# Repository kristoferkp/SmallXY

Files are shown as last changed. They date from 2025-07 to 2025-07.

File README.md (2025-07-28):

# Printer Sugar

### **Work In Progress!**

Printer Sugar is a fast cantilever 3D printer with quality components and a rigid frame.

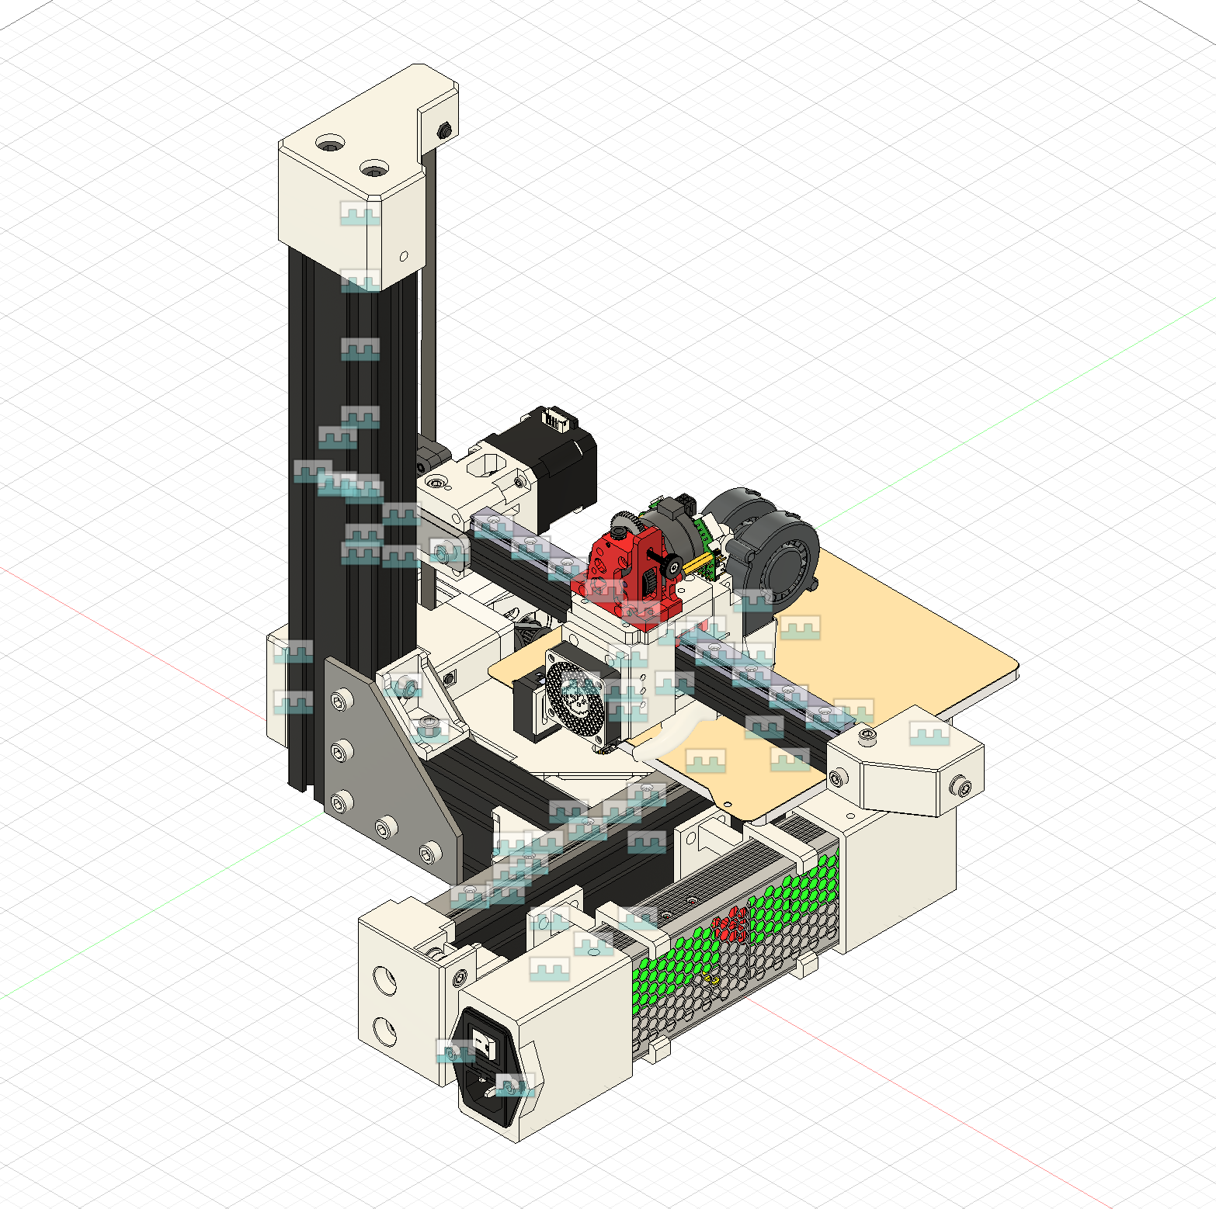
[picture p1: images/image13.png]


## Features
- Cartesian with belted Z
- Compact size
- 180x180x180mm build volume
- Easy to assemble
- No drilling
- Runs Klipper
- Super fast bed meshes with BTT Eddy sensor
- Toolhead CAN board
- Driven by the affordable BTT SKR Pico
- Quality components
- Easy to build

## BOM
|Part|Notes|Qty|Price (EUR)|Shipping|Total Price|Link |
|---|---|---|---|---|---|---|
|TZ V6 2.0 hotend | |1  |15,17 € |0,00 €  |15,17 € |https://www.aliexpress.com/item/1005008625753387.html |
|HGX Lite extruder | |1  |22,45 € |0,00 €  |22,45 € |https://www.aliexpress.com/item/1005008095324836.html |
|Raspberry Pi |already have one on hand |0  |0,00 € |0,00 €  |0,00 € |https://raspberrypi.com |
|BTT SKR Pico 1.0 | |1  |22,63 € |0,00 €  |22,63 € |https://biqu.equipment/products/btt-skr-pico-v1-0?variant=40565262188642 |
|BTT Eddy Coil | |1  |12,76 € |0,00 €  |12,76 € |https://biqu.equipment/products/bigtreetech-eddy?variant=41018205405282 |
|Fystec UCAN |cheaper to buy this with the eddy coil than duo|1  |6,31 € |0,00 €  |6,31 € |https://www.aliexpress.com/item/1005006834027165.html |
|BTT EBB36 | |1  |14,46 € |0,00 €  |14,46 € |https://biqu.equipment/products/bigtreetech-ebb-36-42-can-bus-for-connecting-klipper-expansion-device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|
|5015 Blower Fan | |2  |2,76 € |0,00 €  |5,52 € |https://www.aliexpress.com/item/1005002488988359.html |
|ADXL345 |for bed |1  |2,72 € |0,00 €  |2,72 € |https://www.aliexpress.com/item/1005006825808074.html |
|4010 Fan | |3  |2,51 € |0,00 €  |7,53 € |https://www.aliexpress.com/item/10000382046169.html |
|2M PTFE tube |ID2 OD4 |1  |3,92 € |0,00 €  |3,92 € |https://www.aliexpress.com/item/1005006242932887.html |
|IEC320 C14 |AC-08 |1  |2,37 € |0,00 €  |2,37 € |https://www.aliexpress.com/item/32961436466.html |
|Mean Well UHP-350-24 | |1  |59,12 € |0,00 €  |59,12 € |https://www.digikey.ee/en/products/detail/mean-well-usa-inc/UHP-350-24/7707254 |
|180x180 bed |with magnetic plate |1  |22,58 € |0,00 €  |22,58 € |https://www.aliexpress.com/item/1005005641707683.html |
|MGN15H 250mm | |2  |12,50 € |0,00 €  |25,00 € |https://www.aliexpress.com/item/1000007480470.html |
|MGN12C 250mm | |1  |10,09 € |0,00 €  |10,09 € |https://www.aliexpress.com/item/1000007480470.html |
|Nema 17 motors 40mm |3pcs |1  |45,03 € |0,00 €  |45,03 € |https://www.aliexpress.com/item/1005006568308689.html |
|Silicone spacers 4pcs |16mm |1  |3,14 € |0,00 €  |3,14 € |https://www.aliexpress.com/item/1005001823789355.html |
|GT2 Loop Belt 188mm |6mm width |1  |2,67 € |0,00 €  |2,67 € |https://www.aliexpress.com/item/1005006417199222.html |
|GT2 Loop Belt 650mm |9mm width |1  |2,01 € |4,59 €  |6,60 € |https://www.aliexpress.com/item/32805615376.html |
|5x8x1 shim |comes in a pack of 20 |1  |1,08 € |2,87 €  |3,95 € |https://www.aliexpress.com/item/1005004050860540.html |
|F695 2RS bearings |pack of 10 |1  |6,37 € |0,00 €  |6,37 € |https://www.aliexpress.com/item/32850989216.html |
|GT2 20T pulley 6mm | |1  |4,48 € |0,00 €  |4,48 € |https://www.aliexpress.com/item/32995102911.html |
|GT2 20T idler 9mm | |1  |3,43 € |0,00 €  |3,43 € |https://www.aliexpress.com/item/1005005781354110.html |
|GT2 20T pulley 9mm | |1  |1,35 € |5,04 €  |6,39 € |https://www.aliexpress.com/item/32348909911.html |
|GT2 80T puley 6mm | |1  |4,85 € |2,79 €  |7,64 € |https://www.aliexpress.com/item/1005005585888163.html |
|5x70mm shaft with flat spot| |1  |2,22 € |5,37 €  |7,59 € |https://www.aliexpress.com/item/1005008459963157.html |
|F695ZZ bearing | |1  |3,40 € |0,00 €  |3,40 € |https://www.aliexpress.com/item/1005006822749704.html |
|695ZZ bearing | |1  |3,24 € |0,00 €  |3,24 € |https://www.aliexpress.com/item/4000909556973.html |
|3060 extrusion |350mm |1  |10,57 € |0,00 €  |10,57 € |https://hobby-store.pl/en/aluminium-profile-3060-type-t-slot/altrax-aluminium-profile-3060-t-slot-matt-black.html |
|3060 extrusion |280mm |1  |8,46 € |0,00 €  |8,46 € |https://hobby-store.pl/en/aluminium-profile-3060-type-t-slot/altrax-aluminium-profile-3060-t-slot-matt-black.html |
|3060 extrusion |120mm |1  |3,62 € |0,00 €  |3,62 € |https://hobby-store.pl/en/aluminium-profile-3060-type-t-slot/altrax-aluminium-profile-3060-t-slot-matt-black.html |
|L-type connection plate | |2  |4,00 € |0,00 €  |8,00 € |https://www.aliexpress.com/item/1005008549907378.html |
|T-type connection plate | |1  |4,46 € |0,00 €  |4,46 € |https://www.aliexpress.com/item/1005008549907378.html |
|3030 Corner brackets | |1  |7,56 € |0,00 €  |7,56 € |https://www.aliexpress.com/item/1005007540170351.html |
|M3 countersunk 30mm | |0  |3,69 € |0,00 €  |0,00 € |https://www.aliexpress.com/item/1005007838338973.html |
|M3 screw set | |0  |10,34 € |0,00 €  |0,00 € |https://www.aliexpress.com/item/1005007159750547.html |
|M3 heatset insert |M3x5x4 |0  |3,95 € |0,00 €  |0,00 € |https://www.aliexpress.com/item/1005007973137842.html |
|M3 heatset insert |M3x4.5x5 |0  |2,92 € |0,00 €  |0,00 € |https://www.aliexpress.com/item/1005003582355741.html |
|M5 screw set | |0  |13,36 € |0,00 €  |0,00 € |https://www.aliexpress.com/item/1005007268850289.html |
|M5 50mm | |0  |4,52 € |0,00 €  |0,00 € |https://www.aliexpress.com/item/32810872544.html |
|M6 screw set | |0  |14,75 € |0,00 €  |0,00 € |https://www.aliexpress.com/item/1005007268850289.html |
|M6x12mm | |0  |4,11 € |0,00 €  |0,00 € |https://www.aliexpress.com/item/1005007632215508.html |
|M8 30mm | |0  |3,72 € |0,00 €  |0,00 € |https://www.aliexpress.com/item/32810872544.html |
|3030 M6 t-nuts | |0  |5,58 € |0,00 €  |0,00 € |https://www.aliexpress.com/item/1005007587044629.html |
|2020 M5 t-nuts | |0  |3,13 € |0,00 €  |0,00 € |https://www.aliexpress.com/item/1005007587044629.html |
|Spade crimping kit | |0  |21,92 € |0,00 €  |0,00 € |https://a.aliexpress.com/_EJTbUyW
|16AWG wire | |0  |4,41 € |0,00 €  |0,00 € |https://a.aliexpress.com/_EGvjSkQ
|XH 2.54 kit | |0  |3,41 € |0,00 €  |0,00 € |https://a.aliexpress.com/_EvVOt9y

## Credits
- Big thanks to the Ratrig community and the team behind Ratrig for the inspiration and refrence for the design.
- EVA toolhead community and team for the refrence for my toolhead.
- Voron community for the insipiration of the CoreXY design and refrences.
- BigTreeTech for the refrence parts of their products.
- GrabCAD community for some refrence parts.

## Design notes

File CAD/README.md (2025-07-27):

# CAD files

The f3z is a Autodesk Fusion archive. I would recommend to open it in a new folder as there will be a bunch of files in there when uploaded.

The STEP files are there for compatibility. Do note, that there isn't version history included in the step file.

See the Cantilever files for the design.

## The CoreXY

The CoreXY was not and still isn't finalized. Please do not try to build one as it is incomplete. It is there to show that I actually did something and did not snooze all day.

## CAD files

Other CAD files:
CAD/CoreXY.step
CAD/Cantilever.step
CAD/Cantilever.f3z
CAD/CoreXY.f3z

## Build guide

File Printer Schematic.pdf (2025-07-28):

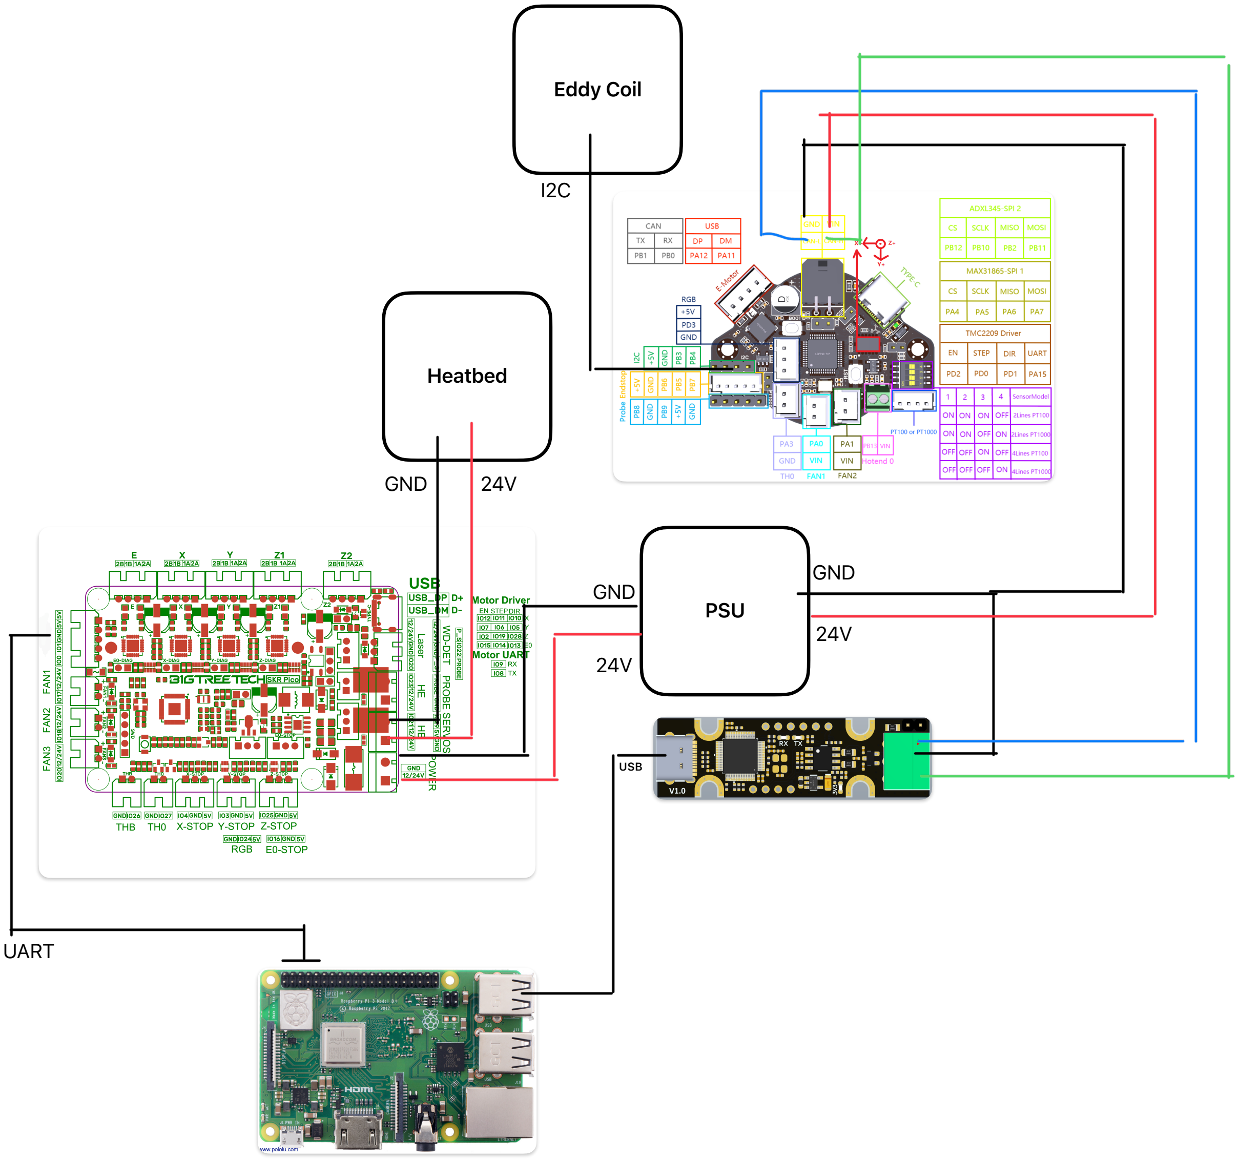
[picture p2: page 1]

USB

UART

PSU

GND

24V

GND

24V

Heatbed

Eddy Coil

I2C

GND 24V

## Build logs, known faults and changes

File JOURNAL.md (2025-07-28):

---
title: "Printer Sugar"
author: "Kristofer P"
description: "A fast and sturdy cantilever 3D printer"
created_at: "2025-07-07"
---

### Total time spent on project at the submitting mark: around 67h

My school doesn't have a 3D printer (well it does but it is a broken Makerbot Replicator) so I wanted to change that. With the 350 USD budget from Hackclub I can design a printer that my fellow schoolmates can use to make their designs come to life.

The after many hours of back and fourth I decided that the printer will use CoreXY kinematics for its great speed and compact size.

# 1st entry: July 7th, 2025: Initial research and frame design.

Researching what parts to include in the 3D printer was a tough challenge to say the least.

First, I wanted to build a small coreXY printer, but after searching for the parts online (mainly AliExpress) and seeing what I already have on hand (basically nothing apart from a Raspberry Pi), I came to the conclusion that it will blow the $350USD budget.

So then, I decided to build a cantilever design for its simplicity and cost.
The main problem that seems to plague cantilever printers is instability.

As I wanted to build a fast machine, hopefully beating the Bambu Lab A1 mini, I decided to use 2040 aluminium extrusion as it is cheap and will probably give it the stability it needs.

I set my target to the Bambu Lab A1 mini. With its 180x180x180mm build volume, my machine would need to match that.

The heatbed options aren't very big on AliExpress (I found very little listings for 180mm heatbeds), so I decided to use a heatbed meant for the Micron+ printer.
There was a option of just using the Bambu Lab A1 mini heatbed unit as its price is very reasonable at €42, but with Bambu being so locked down, I couldn't find any information on it.
It probably is a 24V about 100W heater and some mystery thermistor. I would need to get my hands on one to find out.

I also searched for linear rails and landed on the MGN12H at 250mm long. They should be long enough for the 180mm bed and mounting stress. But I might swap them out for beefier rails down the line.

Found NEMA17 motors that should have enough torque to hold the X-axis up not during use. 17HS4401S.

Chose to use roll-in t-nuts for the linear rails. They are a bit more expensive than drop-in ones, but are way to save the hassle later on when building.

That was the end of the reasearch on that day.

---

I started off by searching for some 2020 and 2040 extrusion. Eyeballed the lengths to be 350mm for the Z, 150mm and 300mm for the bed, 400mm for the X-axis.

The extrusions will be joint together with joining plates. Maybe I will add some other joints, tbd.

Then I added the linear rails. The grabcad model was only 100mm long, so I had to extend it to 250mm. 

I do not know why, but Autodesk Fusion was playing tricks on me the entire time.

For the life of me, I couldn't understand why Fusion was chopping off parts of the entirely different bodies from different compontents.
When I tried splitting the 100mm rail to 50mm, it would split every single rail part and then when I went to delete the extra 50mm, the rail would suddenly have holes in them.

It happend in other areas too, like the extrusions. When I went to extend or cut an extrusion, the other extrusions would cut themself too.
I ended up somehow forcing myself through the problem, so if anyone has some ideas, let me know.

### Time spent on that day: 5h

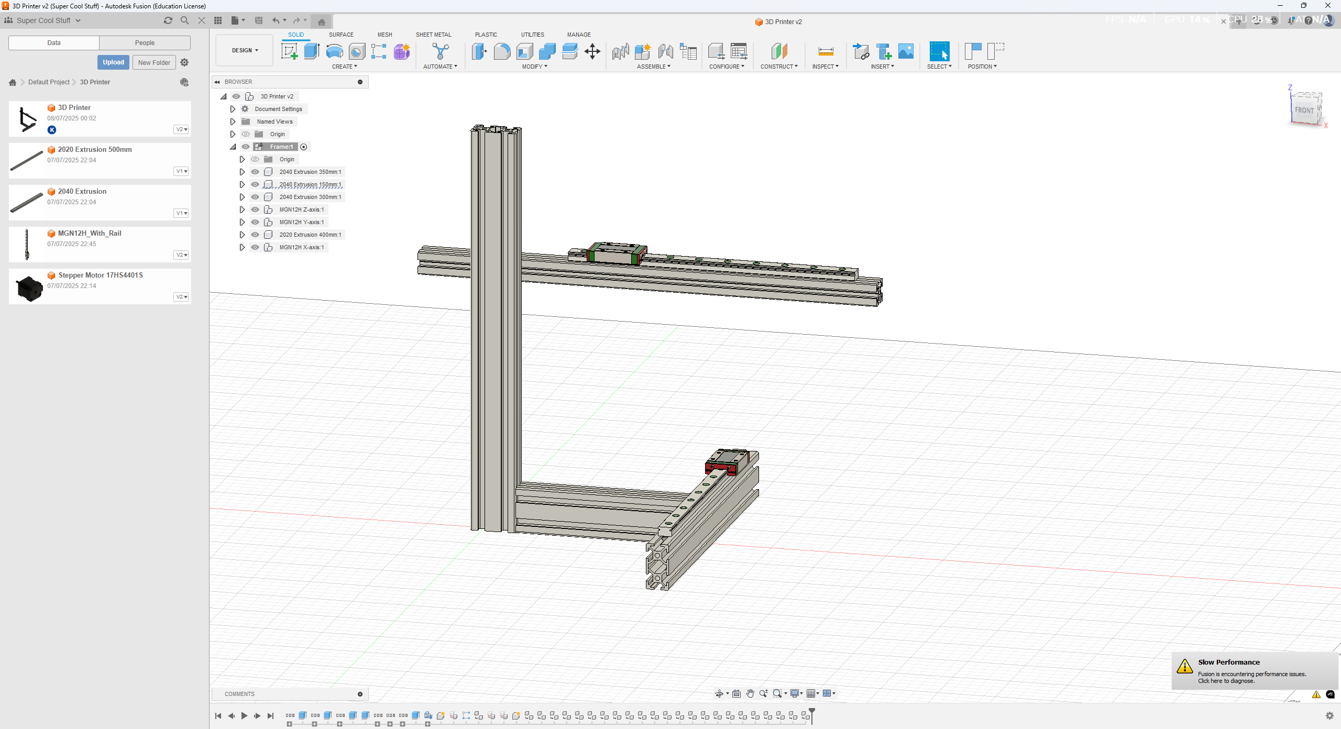
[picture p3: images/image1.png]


# 2nd entry: July 8th, 2025

Did some searching and came to the conclusion, that 2040 extrusion is too flimsy and decided to swap out the extrusions for 3060.
I also searched where I can buy the extrusions and found a Polish shop that sells custom lenghts for a really reasonable price.

3060 for €0.30/cm and 2020 for €0.12/cm.

The bed has been a quite the headache. I can't really make my own bed as I do not have the equipment necessary, so I need to buy one pre-drilled and tapped.

I did find a Ratrig V-minion heatbed assembly, but noone has bought it so it is kinda risky.
The other option I found was the Micron180 heatbed assembly.

It has all the necessary things included for €60, but I might need to swap it out later when I optimize the BOM.

The Micron has a slight flaw for my use case, it is designed to be mounted fixed to the bottom of the printer. Which means, the mounting bracket that goes between the bed and the linear rail carriage has to be huge.

---

I started the day off with replacing the extrusions and fighting with Fusion a bit. I have managed to make sense of the problem a bit, but still kinda wonky.

The rails were next. They were less of an issue, but with the Fusion magic again, I am having a hard time categorizing the models into components. Please do not inspect the components too close.

The mounting brackets were next. I did several designs and L-shaped mounting brackets that I found on that Polish website seems to be the best. I did add a T-shaped bracket to the bottom and normal corner brackets for reinforcment.

I found the CAD model for the Micron180 and just took the bed assembly out of the file. ;)

I did have to modify it, removing the extrusions, making a carrier plate for it, etc.

The carrier plate might actually not warp, I need to learn how the Fusion simulation works.
I have a feeling it will not hold up.

### Time spent on that day: 7h

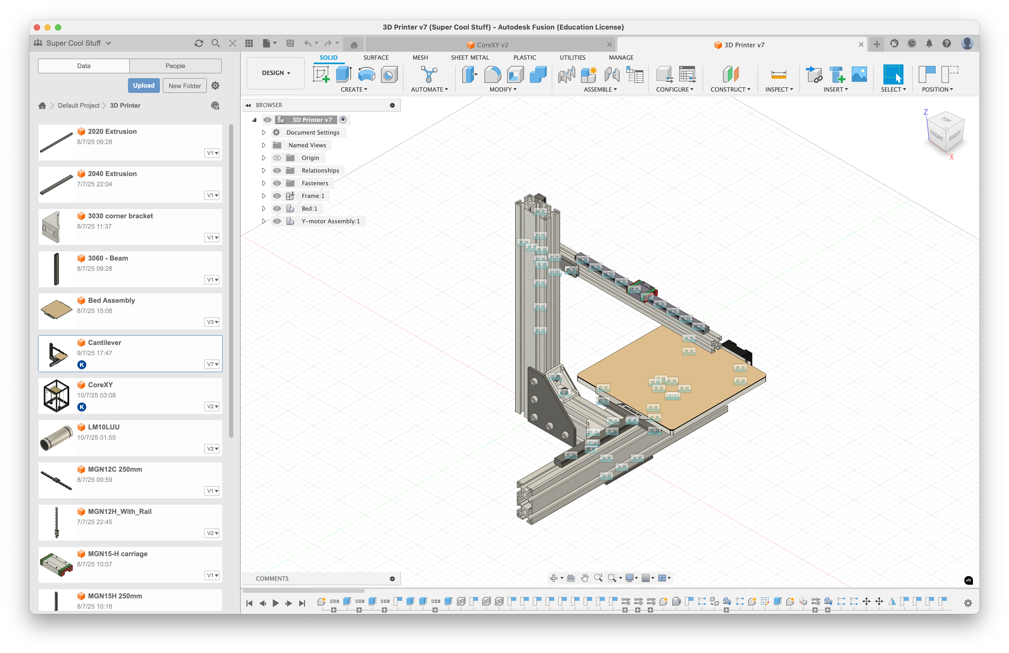
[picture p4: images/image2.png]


# 3rd entry: July 9th, 2025

I started the day researching again.

Looking over the BOM and the design, I think I can build an CoreXY for not a lot more and a lot faster and probably safer design wise.

The bed on the cantilever design is really suspicious.

I decided that I will make a flying bed and not a flying gantry.

The Z will use 4 linear rods and 2 Z-motors with screws.
This is because I only have 2 Z-motor drivers on the board and beacuse it is cheaper.

The Z will use 10mm linear rods, LM10UU and Nema17 motors with lead screws on them.

Hoping to find motors that aren't that expensive.

Found basically Prusa MK3 Z motors with built in 300mm lead screws, will use those.
They come on the printer in a 2 pack too, which is kinda amazing. The stars are slightly aligning.

There is a posibility of using some more Prusa motors. That makes the project a bit more accessable (if someone has MK3 motors lying around).

It is possible to use the MK3 bed and Y-carriage as well, but I don't have them and they are more expensive than the Micron180 bed I want to use.

The beds should be replaceable with a few design tweaks.

I also made the BOM a bit more complete and I am going to have to source a few parts myself beacuse the BOM is offically blown out of budget.

---

I started doing the CAD for the CoreXY printer.

I decided to use 2020 extrusion as there is more of it, so the rigidity shouldn't be a problem, and it is quite a lot cheaper.

The bottom of the printer is under review. I might make a skirt for the electronics or I house the electronics at the back of the printer.

I got the linear rods placed, the bed placed, the NEMA17 motor and its accompanying lead screw and the lead nut placed.
The second linear rods used to connect the lead screw and the Z-axis linear rods were also placed.

Next up I need to make the connecting piece that will be 3D printed.

I have realised that I really do like tinkering in Fusion and researching the parts. It is quite hard, but I like the challenge.

Aimlessly modeling is very time consuming, but when I achive the aim, it gets quite rapid.

### Time spent that day: 8h

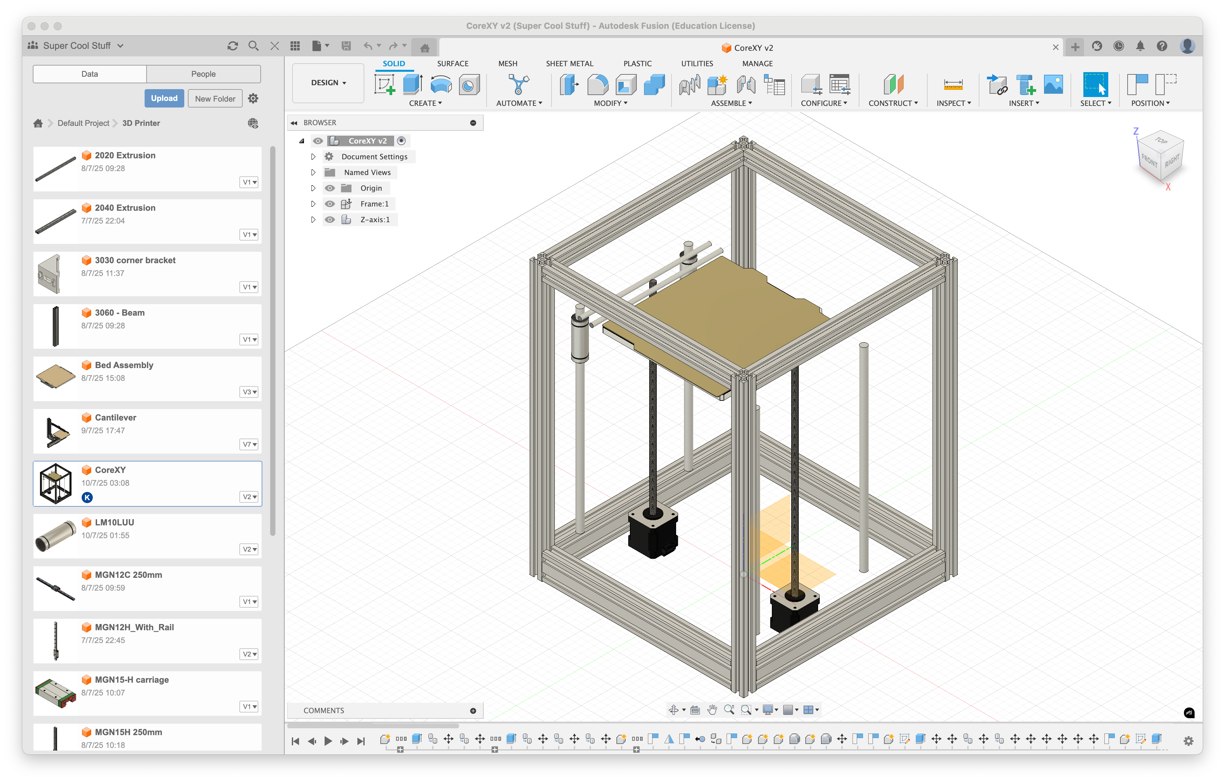
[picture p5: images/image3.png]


# 4th entry: July 10th, 2025

Still thinking about the design of the printer.

The SKR Pico 1.0 that I would like to use beacuse it is so cheap and there is a possibility of using a CAN transiver so you do not have to buy a seperate CAN board.

The SKR Pico has 5 motor drivers - Extruder, X, Y, Z and Z2.

When researching Z axis beds on other printers, I realised that having 3 Z-motors would be advantageous beacuse the bed could trim itself. There would be no need to trim it yourself, just use the Z_TILT_ADJUST in Klipper, just like the Voron Trident.

Then I thought to myself, would I need to swap out the SKR Pico for a board that has drivers for the Z.

But then I realised, if I use a CAN toolhead board, it has a built in TMC2209 for the extruder - I don't need the extruder driver on the board anymore, so I can use that for the 3rd Z motor.
I did some searching (asking AI) and it is indeed feasable.

I then decided to change out the Z axis design again for the Voron Trident design.

I went to the Trident configurator and for a build size of 180mm^3 it recommended me the frame size of 340x340x430mm - basically the frame size I was already using.

I searched a lot on aliexpress too. I think I had over 100 tabs open at the same time (thank you Zen browser for saving me a bit).

I went down a different rabbit hole of "what if I pivot again and build a cartesian?" but that I shut down as there isn't really any reason to pivot again.

I searched about all the different motors out there. There are a lot of them.

But they have quite awful shipping times. If I buy them now, it will take almost a month to get to me. This is also the reason why I am crunching so hard. Time is of the essense.

I watched a cool video about how to build a 3D printer, it is a bit old at this point (5 years at the time of writing), but still quite a good watch. 
[How to Build a 3D Printer (The Ultimate Guide)](https://www.youtube.com/watch?v=qub5chyIQ0s&t=5674s)

I was really worried about the shipping costs on the motors. They ballooned way out of porpotion. 
I was really doubting if there are any cheap motors out there, but then I found Robotdigg.

It is quite a cool site and they had the motors with lead screws that I needed, the shipping was around 30 euros.

I wasn't satisfied yet. Over 120 euros just for Z-axis motors is just too much on a somewhat budget printer.

I had my eye out for the motors on the BOM, but there was a small issue - I could only buy one.
That made me search for better option, but there weren't any and then I circled back to these.

I do not know what kind of trickery AliExpress does some times, but when I opened the tab in incognito, I finally was able to buy more than one.

The price is around 4 euros more, but I would have liked an option to discard that promotion so I could buy more of them.
There should have been a pop up that said "Hey, I see you are trying to buy more than 1, would you like to get rid of that exclusive offer?"

But I digress, I finally got some cheaper motors for the Z-axis but the tomfoolery wasn't done just yet.

The A/B motors were also quite the challenge. I searched far and wide for the motors that ended up in my BOM, none were quite good enough. Not enough torque, too hi inductance, not enough current, etc.

There was the shipping problem here as well. As soon as you ordered more than one, the shippiing shot up to around 30 euros. This was double the price of the motors together, so I had to find some other ways.

The way ended up pretty simple. Find some that come in a pack. This eliminates the shipping cost on pretty much in all cases.

I found the 17HE19-2004S motors. They are powerful, have a pretty low inductance and are cheap. They only come in a pack of 3, not 2 that are needed - so I guess one is extra just in case.

---

I started the CAD redesign by removing everything. This day has been heavy on the modelling side.

I remade the entire frame. Slightly modified the dimensions. 

I added the backbrace to the frame for the 3rd Z motor.

I added the linear rails, the stepper motors with the lead screws.

I added the bed, the aluminum braces under it.

I did take the bed holder mechanism from the Voron Trident, very many thanks to the team and the contributers that make that project happen.

As my bed is quite a lot smaller than the Voron Trident's bed, I had to modify half the mechanism to work with my smaller bed as there is enough room for the big and bulky mechanism.

Should have I made the frame bigger? I guess we have to find out.

The margins on the parts are still quite small, maybe even hitting the aluminum bed, I will have to find out when I build the machine and modify it a bit.

Added 3-way corner connectors to the build.

Started designing the gantry.

### Total time spent that day: 8h

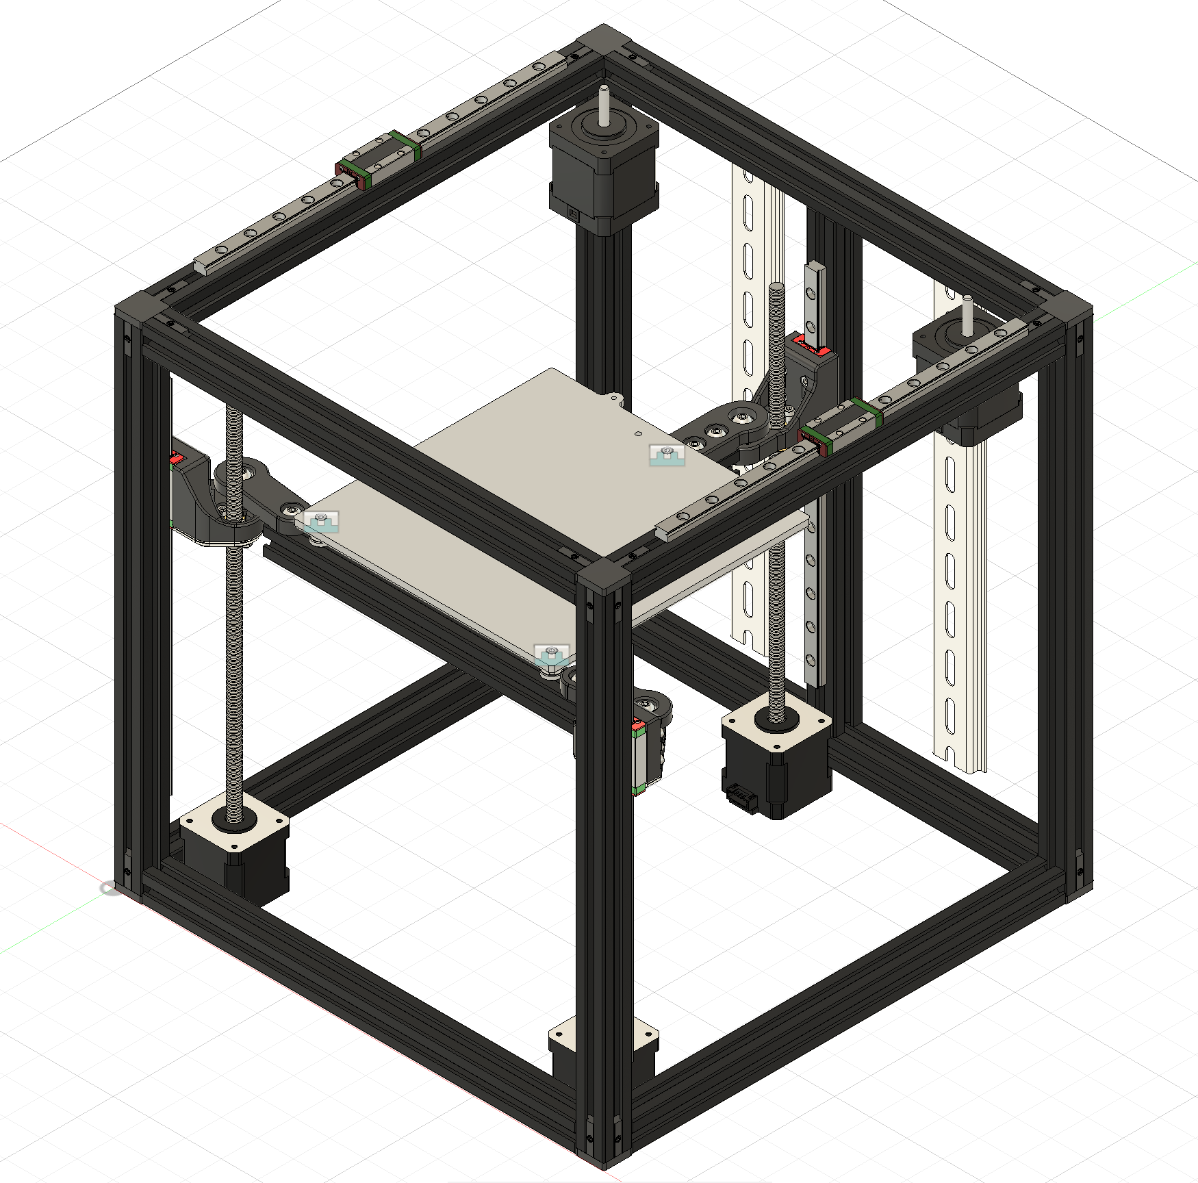
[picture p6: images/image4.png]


# 5th entry: July 11th, 2025

Oh how many different options. I started questioning the corner connectors. Are they even good for a 3D printer? Are these the better option?

I didn't want to use blind joints as they require drilling new holes into the extrusion that I am personally not confortable doing. I could figure it out but I don't want to risk it.

Then I saw the openbuilds corner cubes. They seem good and sturdy. Tapping the ends of the extrusions doesn't seem all that difficult. I was ready to add them to the design when I found out how expensive they are.

I mean they aren't that expensive, but still are quite a bit more expensive than just using corner brackets.

I have to use corner brackets anyway for the bed frame so might as well use them all throughout.

20pcs with hardware is 12 euros as supposed to corner cubes with are 14 euros for 8pcs.

---

I started by replacing all the frame extrusions again. I saw that there are differences from extrusion manufacturer to another in [a YouTube video about blind joints](https://youtu.be/2dvbn0rWA60).

I found the technical drawings of the manufacturer on the [Polish webstore where I found the extrusions](https://hobby-store.pl/) and I started to create a sketch, made almost halfway to a finished sketch and then I found they just have a 3D model available...

I downloaded it and replaced all extrusions on the design with the new one. They are indeed different but not by much and I really doubt it was neccessary.

Started making the gantry.

### Total time spent that day: 5h

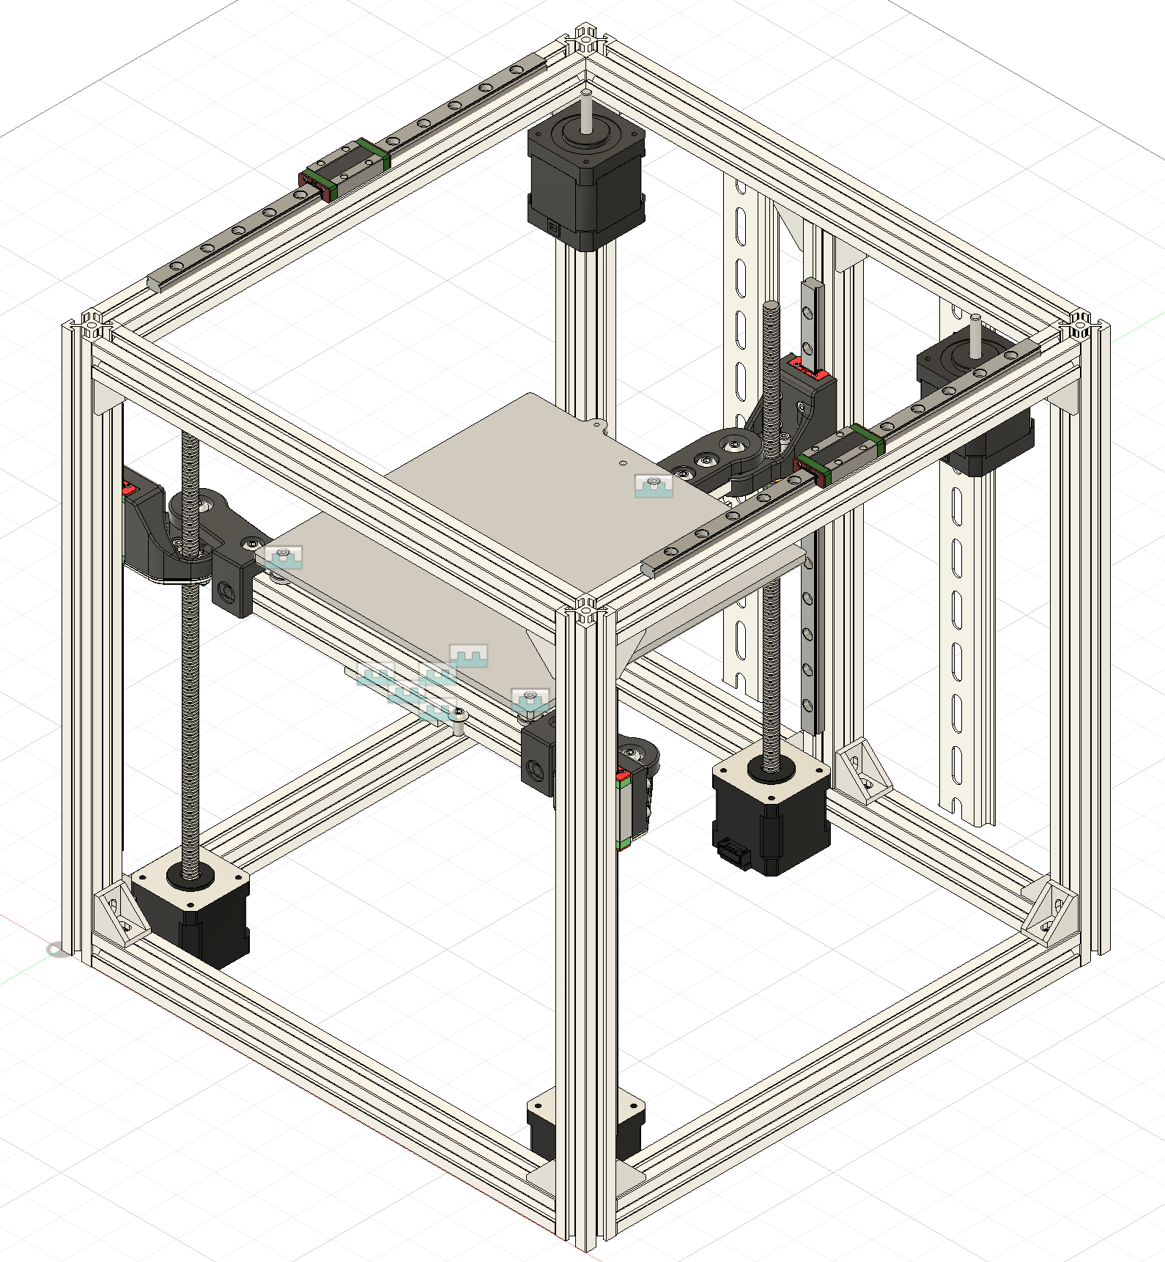
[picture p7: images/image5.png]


# 6th entry: July 12th, 2025

Today started off different. No researching, just modelling.

Made the X-gantry belt/extrusion holder.
It was actually not that bad. I found models for heatset inserts, F695 bearings.

The real complexity came when I finished the gantry and noticed that I do not have enough room in front of the bed for the toolhead.

As I want to use the eddy probe and use the tapping functionality in the [eddy-ng project](https://github.com/vvuk/eddy-ng), the toolhead needs to fit over the bed.

This would not have been possible with the current design, so I needed to make the frame bigger.

This meant a lot of backtracking and modifying the existing design.

Uhmm, this is kinda weird. After coming back to this, I got recommended a ModBot YouTube video exactly about eddy-ng. Perhaps he saw the project the same way I did, Voron discord server.

The A/B motors mounts were next. They were pretty complex, I am doubting my abilities to create a working model, but when I get my hands on the parts and assemble it, I can tweak the models.

I had to figure out how to make the belt tensioner. I first thought of a way where the motors move, but then I thought of a system where the front pulleys get pulled closer to the front.

When I had done those, I went and made the electronics bay. I found a model of MeanWell PSU I am planning to use, but as the electronics bay uses DIN rails, the mounts are easily interchangeable.

The diary entries get shorter and shorter as I have less and less time, but I still have managed to crunch my way through. I just need to make the toolhead, finish the electronics and the BOM.

I want to add a nozzle scruber to the bed assembly too, but that stage comes a bit later.

That is about it for today. I kinda need to fix my sleep schedule, all these late night CAD sessions aren't probably good for me.

### Total time spent that day: 8h

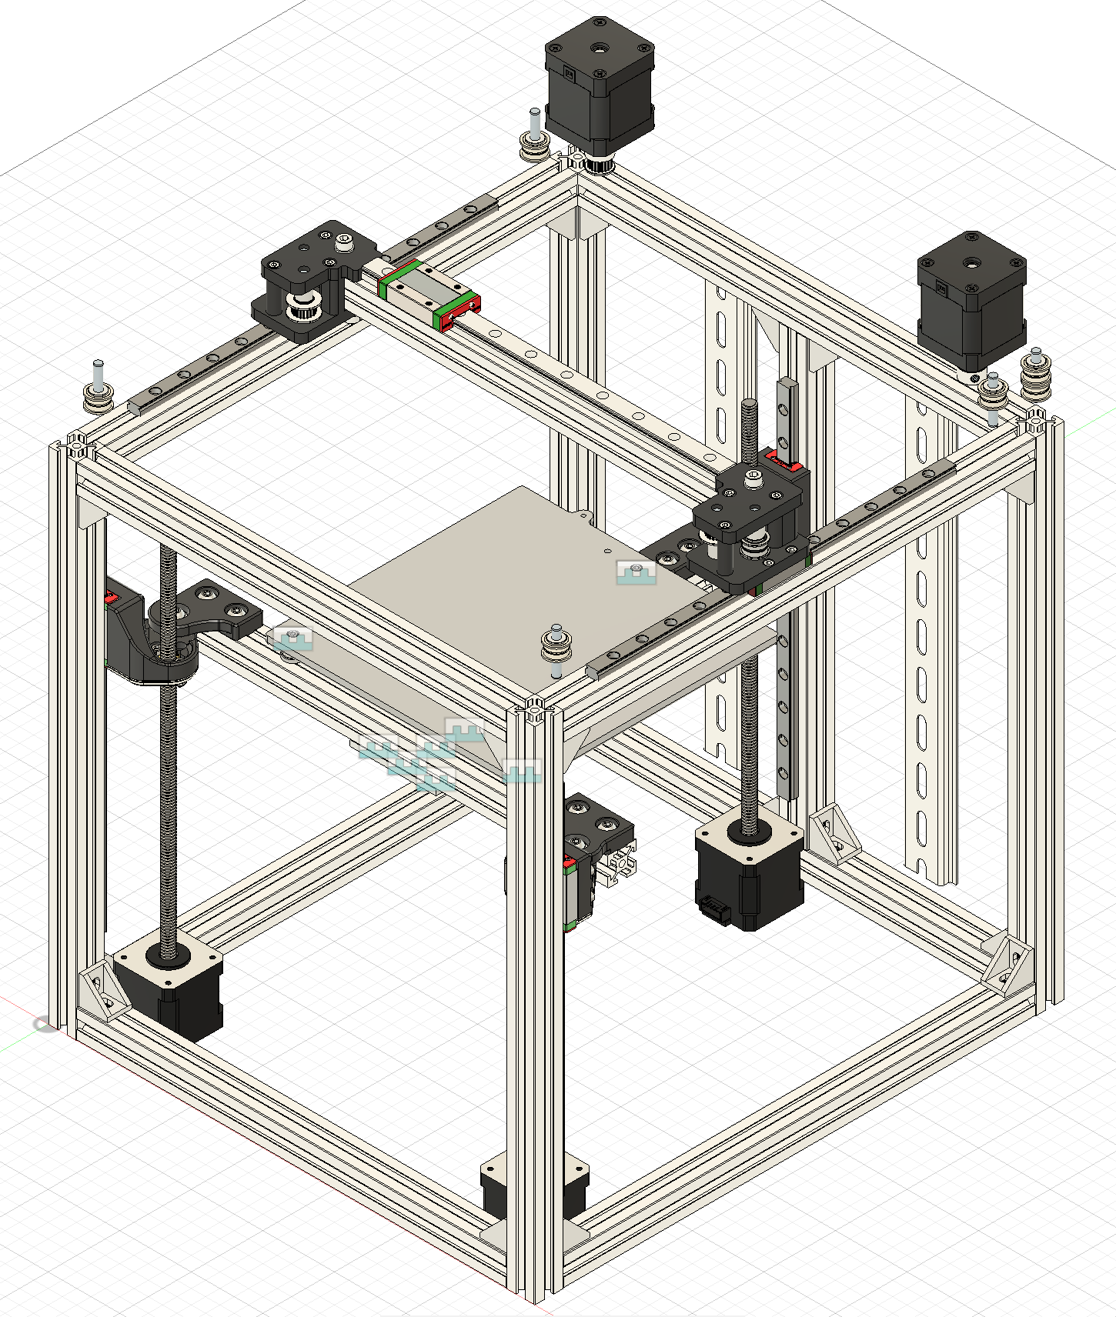
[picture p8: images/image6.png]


# 7th entry: July 13th, 2025

Finished the CoreXY printer, but when looking over the BOM it is really expensive. I might choose to change it out to cartesian platform or even go back to cantilever.

Spent a lot of time researching on how to make the CoreXY cheaper, but to no avail. Still seems too expensive.

After that I made the decision to move to a cartesian platform.

I made the frame out of 3030 extrusion for the cartesian printer, but the problem is joining the extrusions together, the frame needs blind joints, but I do not know if I can do it. Would love it if I didn't have to do blind joints.

Need to reaserch a bit more.

### Total time spent that day: 2h

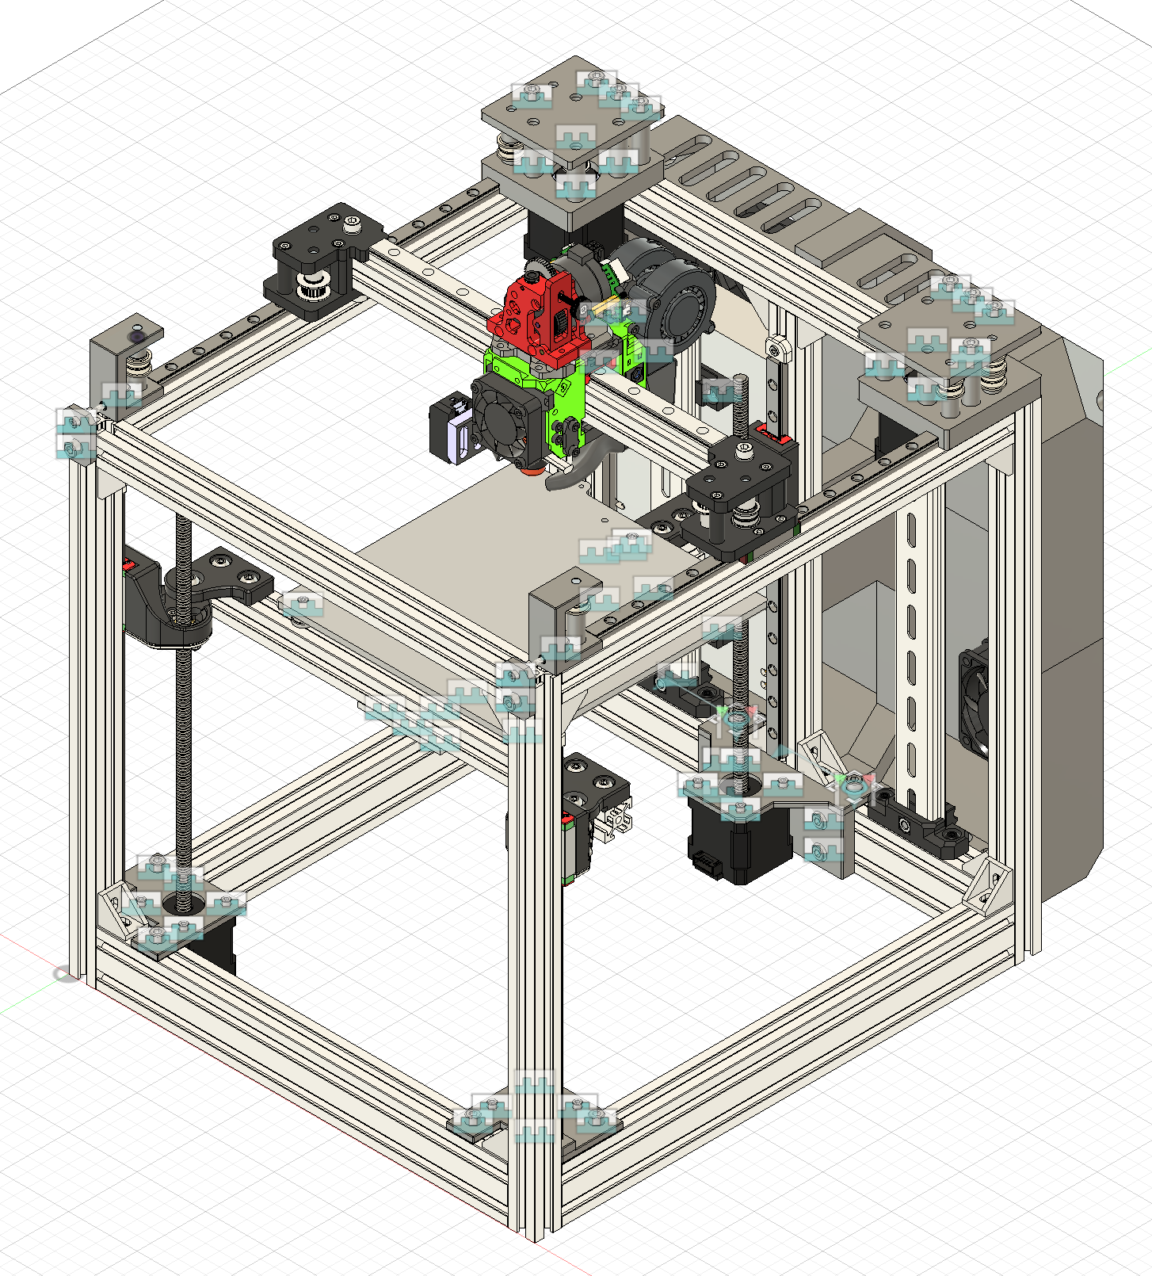
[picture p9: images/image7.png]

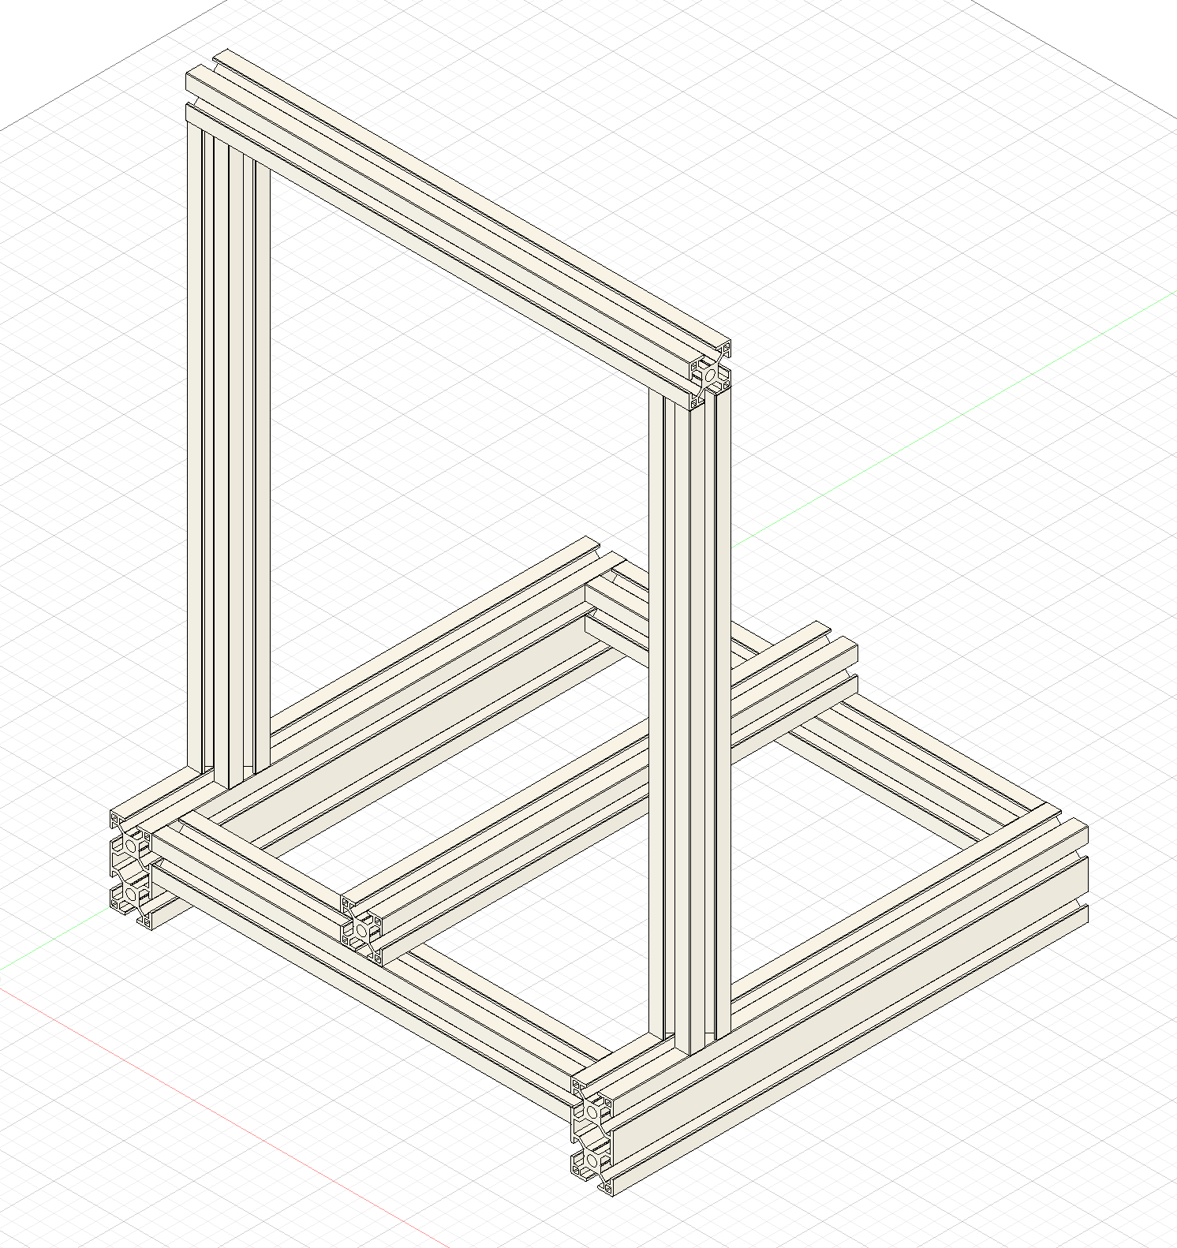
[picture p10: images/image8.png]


# 8th entry: July 14th, 2025

Started with research. How do save costs on a 3D printer while still maintaining speed?

Saw that the RatRig V-minion is a good printer with good speed, but it is not available anymore and is a bit too expensive.

Decided to make a cantilever design inspiried by the V-minion. I do not like that it has a lead screw Z and would like to make the electronics mount on the printer and not be on a seperate box.

### Total time spent that day: 2h

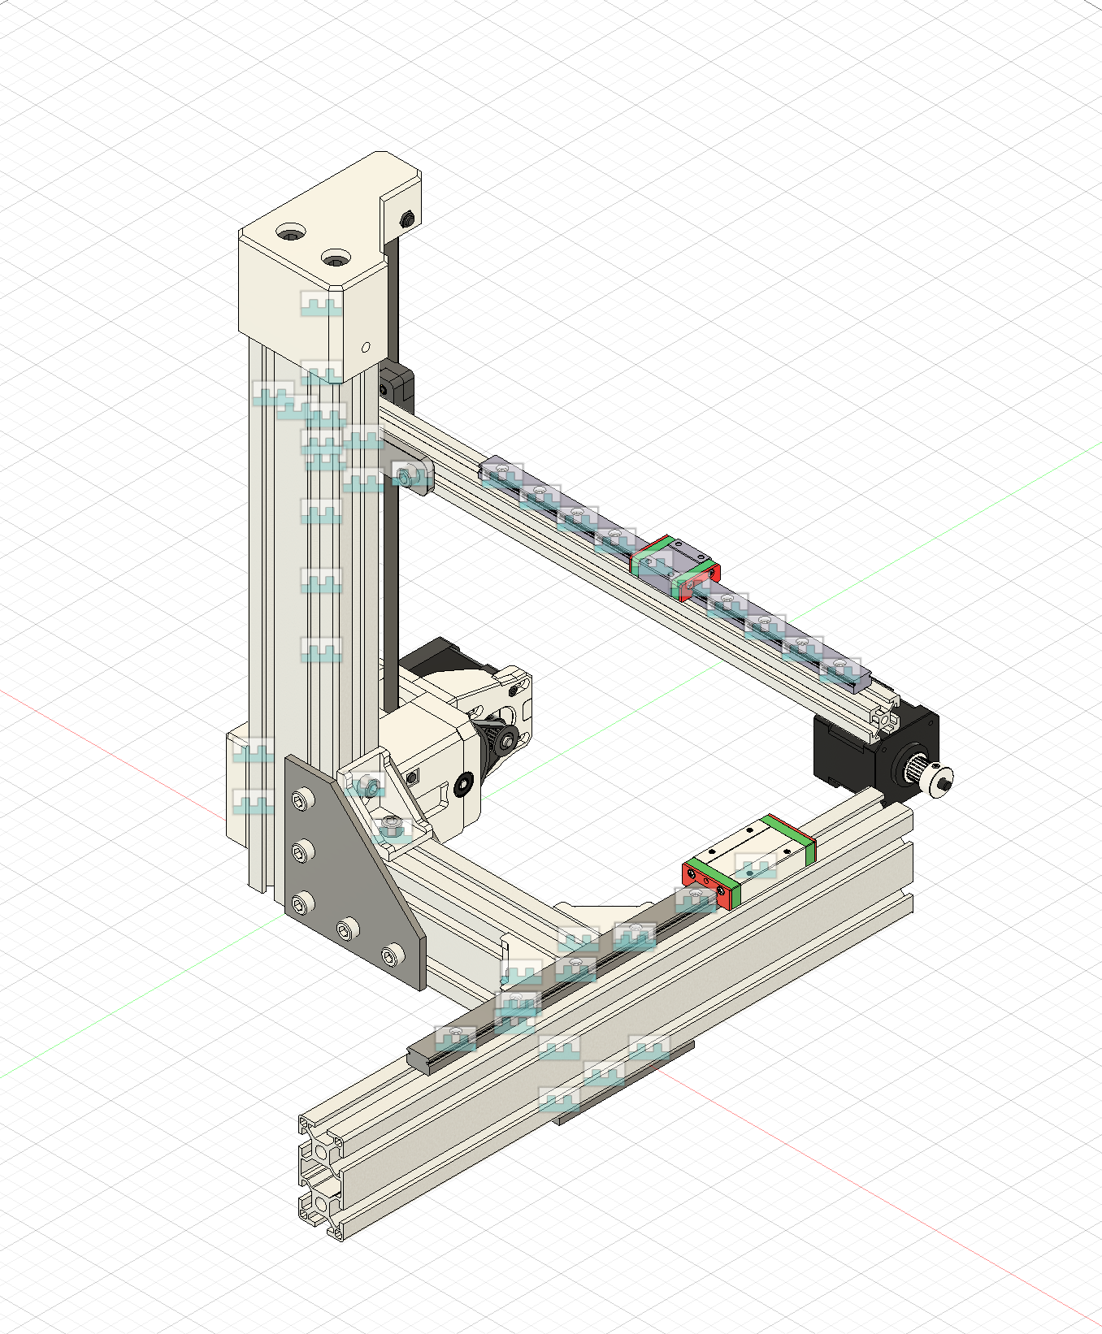
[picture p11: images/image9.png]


# 9th entry: July 15th, 2025

Made some improvements to the printer. The Z axis is belted, the bed is still 180x180mm big, but the footprint is smaller.

Started making the z axis and bed. 

Saw from the Micron180 that the Z-axis should have a gearbox of some sorts to stop the X-axis dropping down.

Decided to make the gearbox similar to the one on the Micron. I will adapt that onto the cantilever printer.

The bed was quite simple. I found a 180x180mm bed for cheap. The Lerdge iX print bed. Its heatbed is only about 25 euros and has the mounting holes close together, so the plate under it doesn't need to be that big. 

The problem with the bed is that it is quite thin and doesn't have the power of a silicone heater, but I think that it will be good enough.

The plate should be made from aluminium, but that is quite expesive, so I think I will try and make it using carbon fiber infused filament.

Search for suitable filaments and found the PLA-CF from Bambu Lab. It doesn't have the bending modulus of something like Nylon, but it is pretty close.

Bending modulus is the bending force the filament can withstand - or so I think.

I just need to add some silicone spacers so the hot bed doesn't touch the plate. Might still need to make the plate out of aluminium if this doesn't work.

I uploaded the plate design to JLCCNC and the quote was around 20 euros plus shipping. Not too bad, but that still would eat into my budget more than I would like it to.

I found the JLCMC website, even though I have ordered from JLCPCB in the past, never have my eyes wondered so far that I find this website. Looks cheaper than AliExpress but I will have to search this site longer at a later date.

I can get a whole Voron 2.4 350mm spec frame for 20 EUROS! My jaw dropped when I saw that.
Literally a similar frame on AliExpress is 77 euro. Holy moly. What a find. 

The best part is the global direct line shipping took me like under a week the last time I ordered from JLCPCB. I have to find out more about this website.

### Total time spent that day: 2h

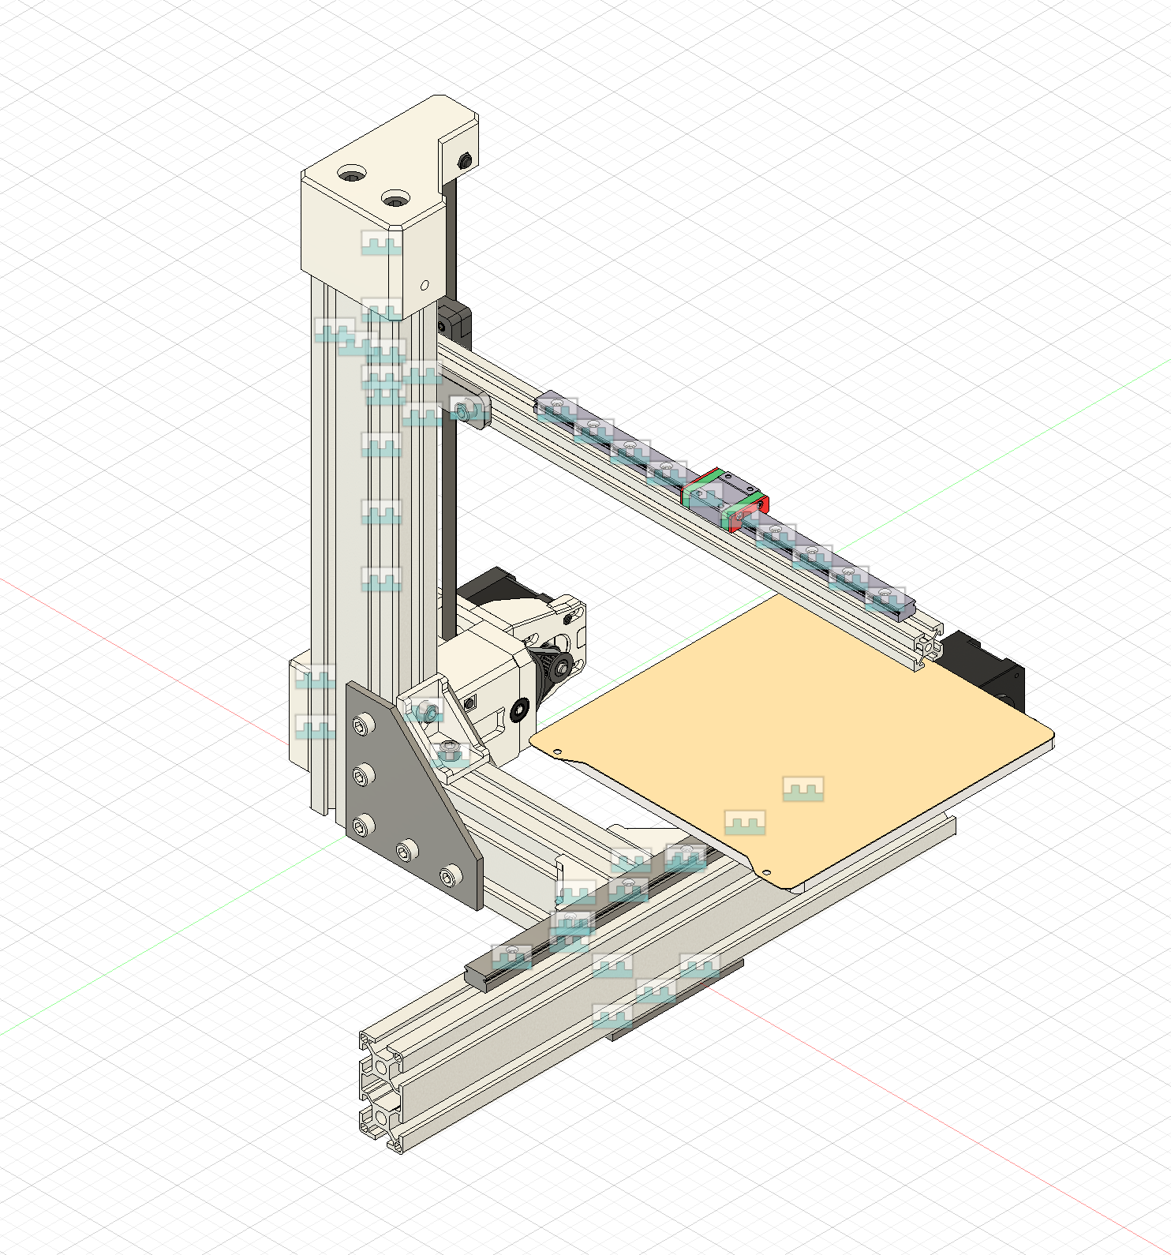
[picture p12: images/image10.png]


# 10th entry: July 16th, 2025

Today we got back to grinding.

Made/finished the Z-axis design. The Z-axis uses a 20T-80T gearbox, so the gear ratio is 4:1. This should be enough to hold the printer up. If not, I could switch the 20T out for a 16T for a 5:1 gear ratio.

Made the Y-axis parts, like the motor mount, idler mount and plate mount. The plate is quite sketchy, but if something ends up being wrong after I send it to JLCCNC then I'd be screwed. So I will try the printed plate and if that fails, I will get a aluminium plate.

Added a few things to the BOM, like the bearings and other knick-knacks.

Almost finished design. I just need to make the X-axis and toolhead.
I wanted to just use the EVA3 toolhead system, but we aren't allowed to just copy parts, so I will make my own.

The printer is almost ready. I need to finish it fast as the shipping times get longer and longer. 

Oh, and also need to make the electronics bay.

It really is a race against the clock.

### Total time spent that day: 6h

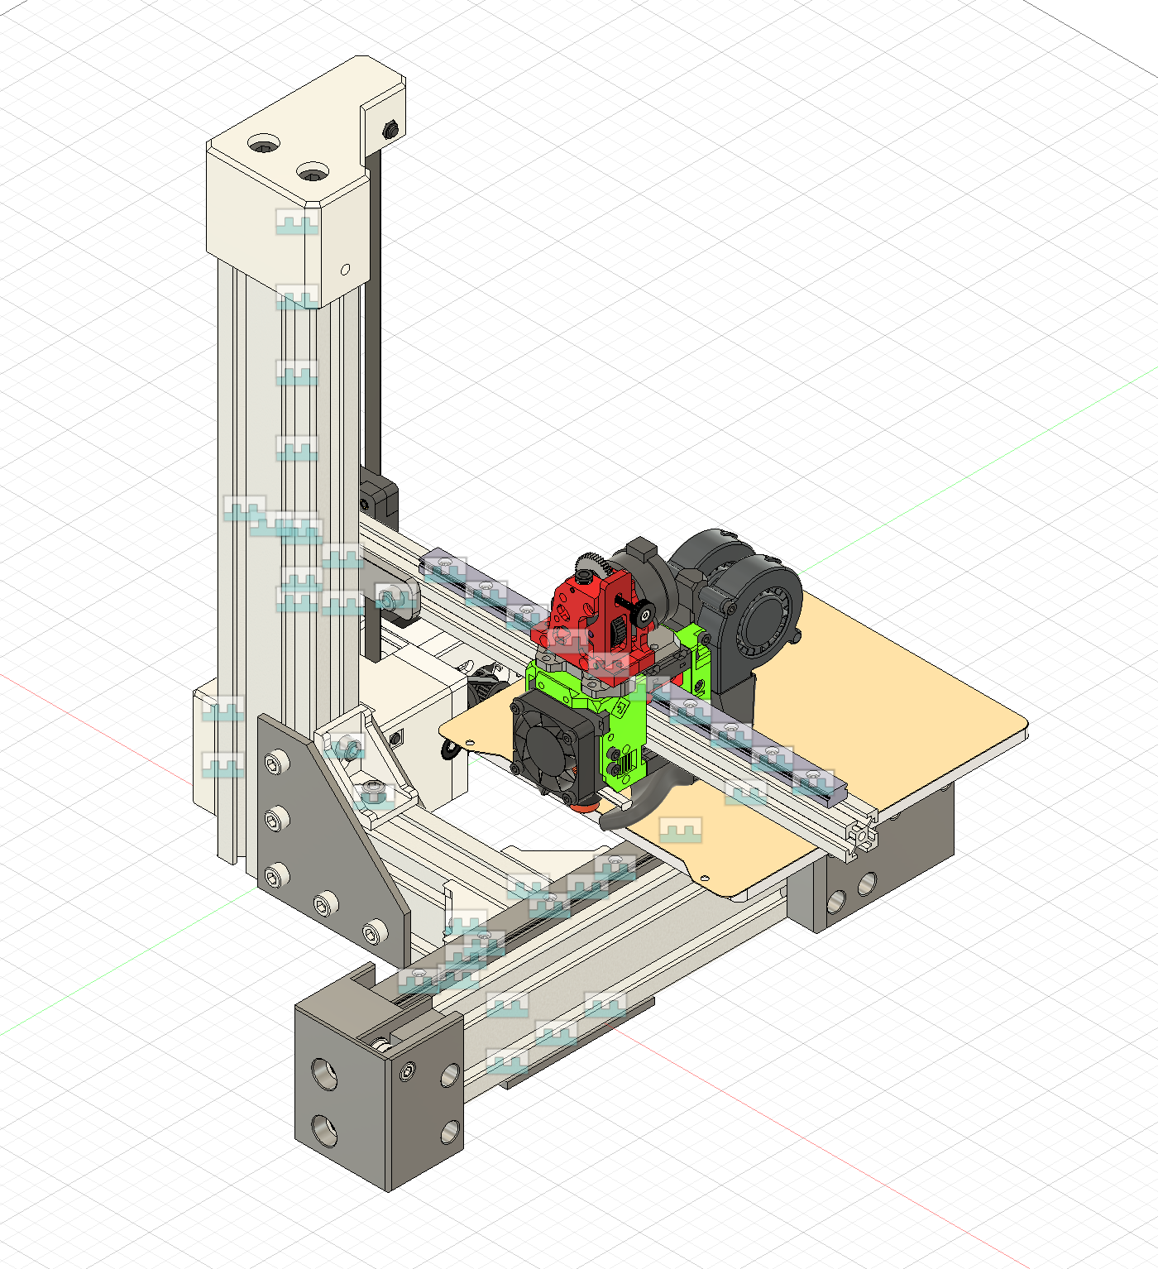
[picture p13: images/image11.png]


# 11th entry, July 17th, 2025

The day has been mostly designing, but also reasearching different hotend options. I had already picked out the TZ V6 hotend, but I wanted to see what other options there are. 
There aren't a lot of hotends that specify how much plastic they can push through, so that makes it a lot harder.

The EVA toolhead is a refrence, it will be replaced by my design.

I did end up just sticking with the TZ V6.

I designed a toolhead too. The main inspiration is the EVA toolhead, as I like the modularity it offers if I decide to swap things out.

The hotend is cooled with a 4010 axial fan to minimize heat creep and the part cooling is using two 5015 blower fans.

It probably is a bit overkill, but I want to make the printer go brrr fast and I need to cool the part fast for that.

### Total time spent that day: 8h

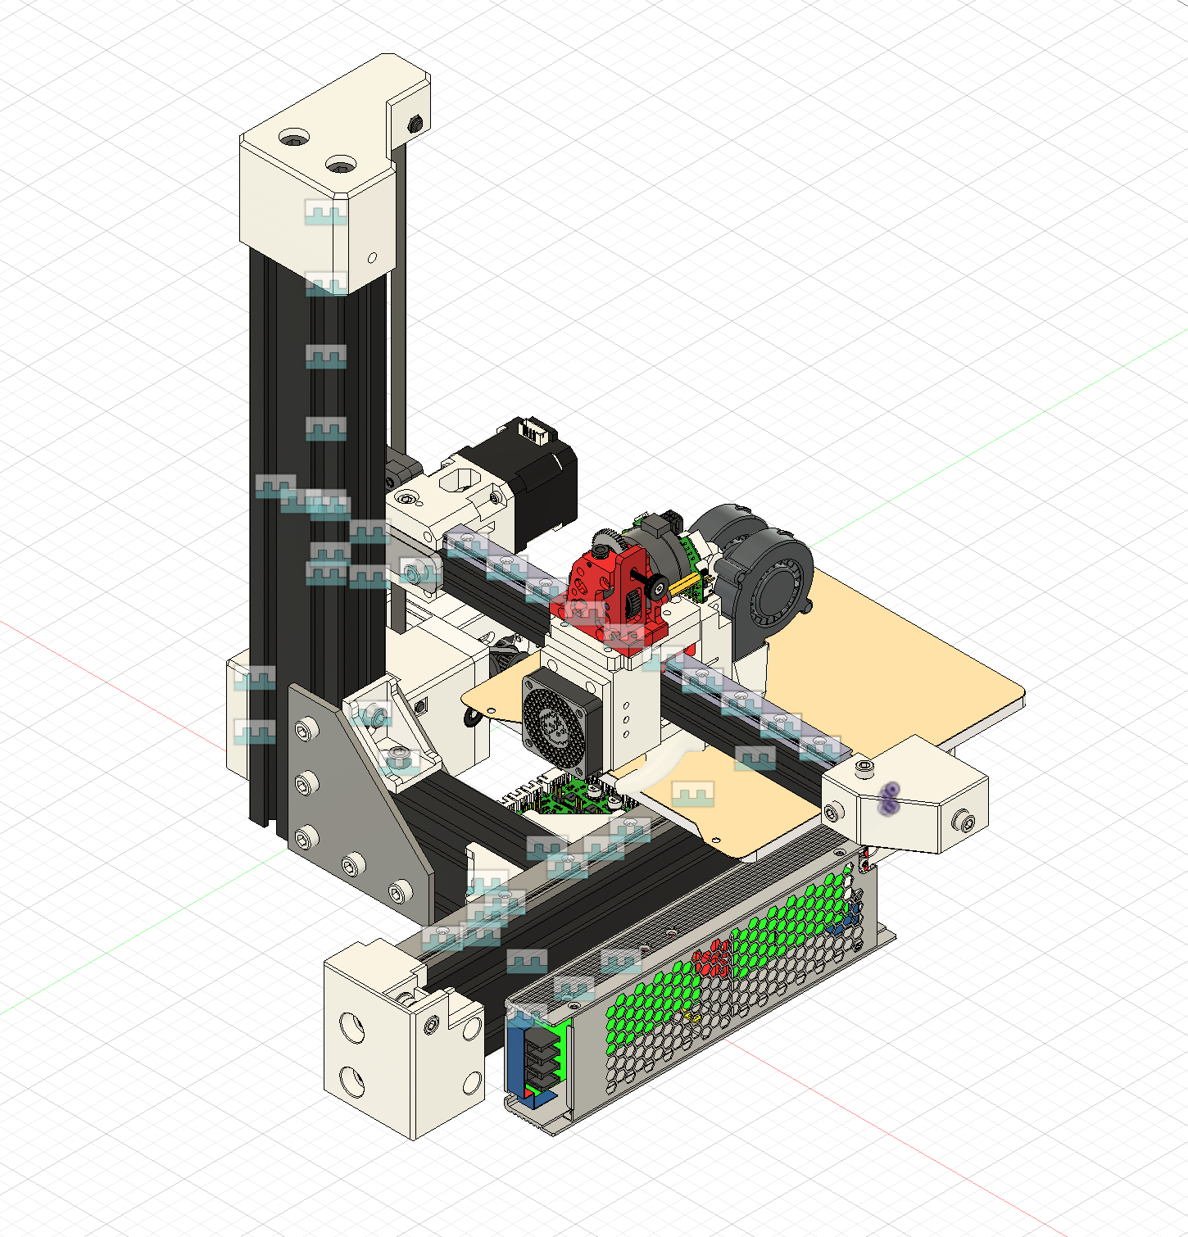
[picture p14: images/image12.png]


# 12th entry: July 27th, 2025

I have been really really busy and haven't had much time to finish the design, which is sad as I do not have enough time to build it before the 7th of August.

I need to check over my PC as Fusion is really really slow and it is really hard to design.

The printer is done. I have finally finished it.

Today I did the electronics box, the PSU mount, finished the toolhead, all the other bits and pieces.

The electronics box was harder than I expected as I do not have anything to base the design off of in the real world. Is 50mm of clearence enough or do I need more? Can I make I smaller, etc.

It has been quite the journey and I have learnt a lot. This is the first printer I have designed and it shows. I have taken inspiration from already made printers in the hope of not burning anything down and making sure everything works.

The only challenge now is to make it in real life and to tweak and tinker with the design even more to finalize the design. 

I need to look over the BOM and sumbit it.

### Total time spent that day: 6h


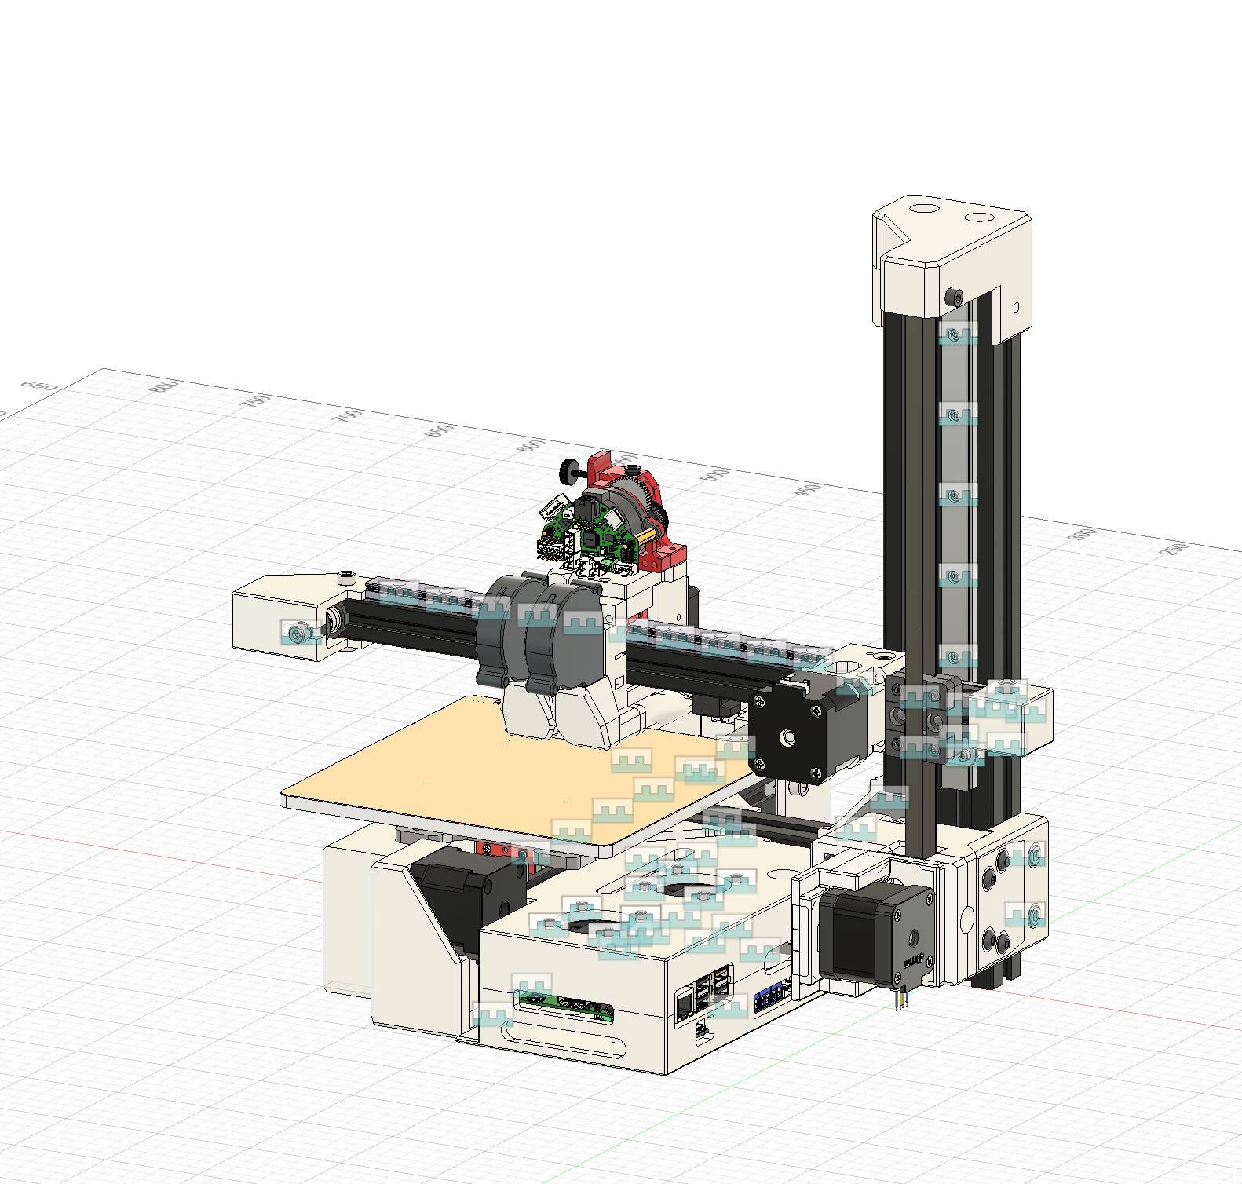
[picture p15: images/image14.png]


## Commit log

2025-07-27 almost final
    [BOM.csv]
2025-07-27 big files
    [Cantilever.f3z, Cantilever.step, CoreXY.f3z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]
2025-07-28 Update BOM.csv
    manually edited
    [BOM.csv]
2025-07-28 Update BOM.csv
    hand typed
    [BOM.csv]
2025-07-28 added wiring
2025-08-02 Update BOM.csv
    trying to fix csv file
    [BOM.csv]
